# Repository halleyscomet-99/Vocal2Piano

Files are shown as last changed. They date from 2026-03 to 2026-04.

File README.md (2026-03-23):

# Vocal2Piano

An external piano exoskeleton that enables real-time robotic accompaniment by tracking and transcribing vocal performances into physical key strikes.

## System diagram

System diagram

## How it works

1. **Vocal2MIDI_live** listens to a microphone and converts pitch to MIDI in real time. Three modes: single-note melody instrument, singing/voice, or polyphonic chord input.

2. **Vocal2MIDI_file** takes an uploaded audio file, separates vocals from accompaniment if needed (via Demucs), then transcribes to MIDI (via Basic Pitch ONNX).

3. **MIDI2Chords** reads the live melody notes, figures out the key, picks a chord that fits, and sends voicing targets for each board.

4. **MIDI2Piano** takes those chord notes, works out where each board needs to slide to cover them, and sends `MOVE` / `FIRE` commands to the Teensy over USB serial.

5. **Teensy 4.1** moves the two stepper motors and fires the solenoids.

6. **Max/MSP patch** shows the detected notes and key on a visual keyboard in real time, connected to the Vocal2MIDI_live MIDI virtual port.

7. **Web frontend** lets you record live, upload files, see the pipeline status, and play back original vs MIDI side by side.

## Repository structure

```
Vocal2Piano/
├── software/              Python pipeline + React web UI
│   ├── app/               React/Vite frontend
│   ├── engine/            Python scripts
│   │   ├── Vocal2MIDI_live.py
│   │   ├── Vocal2MIDI_file.py
│   │   ├── MIDI2Chords.py
│   │   └── MIDI2Piano.py
│   ├── files/
│   │   ├── input/         uploaded audio (git-ignored)
│   │   └── output/        generated MIDI + stems (git-ignored)
│   └── patch/
│       └── Vocal2MIDI.maxpat    Max/MSP visualization patch
│
├── firmware/              Teensy 4.1 firmware (PlatformIO / C++)
│   ├── platformio.ini
│   └── src/main.cpp
│
└── hardware/
    ├── pcb/               KiCad design files, gerbers, BOM
    └── cad/               Mechanical design, 3D print files
```

## Quick start

### Requirements

- Python 3.11
- Node.js 18+
- PlatformIO CLI

### Python environment

```bash
cd Vocal2Piano
python3.11 -m venv .venv
source .venv/bin/activate

pip install sounddevice aubio librosa scipy python-rtmidi websockets
pip install 'basic-pitch[onnx]' onnxruntime
pip install fastapi uvicorn python-multipart
pip install demucs
pip install pyserial

# optional — better live pitch accuracy
pip install crepe tensorflow
```

### Frontend

```bash
cd software/app
npm install
cp .env.example .env    # set VITE_BACKEND_URL=http://localhost:8000
npm run dev             # opens at http://localhost:3000
```

### Firmware

```bash
cd firmware
pip install platformio
pio run --target upload
pio device monitor --baud 115200
# should print: Voice2Piano Teensy ready
```

### Running the full system

Open four terminals:

```bash
# 1 — file conversion server (File tab in web UI)
source .venv/bin/activate
python software/engine/Vocal2MIDI_file.py --server

# 2 — live pitch detection (match the mode selected in the UI)
python software/engine/Vocal2MIDI_live.py --mode instrument --ws
# or: --mode voice  (singing)
# or: --mode chord  (chords/accompaniment)

# 3 — chord generation
python software/engine/MIDI2Chords.py

# 4 — sends commands to Teensy
python software/engine/MIDI2Piano.py --live
```

Open `http://localhost:3000`.

For Max/MSP: open `software/patch/Vocal2MIDI.maxpat`, set the MIDI input to `Voice2Piano_Layer1`.

## Hardware

Two driver boards (15 solenoids each) slide on independent linear rails driven by NEMA17 steppers via TMC2209 drivers. A Teensy 4.1 controls both boards and both motors over a single USB connection.

### PCB

See [`hardware/pcb/README.md`](hardware/pcb/README.md) for fabrication files, BOM, and assembly instructions.

### CAD / Mechanical

See [`hardware/cad/README.md`](hardware/cad/README.md) for the full mechanical design, system animation, and 3D printable parts with print settings.

## Calibrating rail movement

After flashing the firmware, check that the boards move the right distance:

```bash
# in the Teensy serial monitor:
HOME
MOVE R 12 100
```

Measure the actual travel. It should be 12 × the semitone spacing on your piano (roughly 164mm). If it's off, adjust `STEPS_PER_SEMITONE` in `firmware/src/main.cpp` and reflash.

## Training on real music

MIDI2Chords ships with hand-tuned chord transition weights. To replace them with weights learned from actual MIDI files:

```bash
python software/engine/MIDI2Chords.py --train software/files/input/
# writes learned_transitions.json, loaded automatically next run
```

## Author

Chenwan Halley Zhong — MS Robotics, Northwestern University

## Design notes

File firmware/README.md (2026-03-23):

# Firmware

Teensy 4.1 firmware. Receives serial commands from `MIDI2Piano.py` and controls two solenoid driver boards and two stepper motors.

Built with [PlatformIO](https://platformio.org/).

## Build and flash

```bash
pip install platformio
cd firmware
pio run --target upload
pio device monitor --baud 115200
```

If VS Code shows red squiggles on the includes, run `pio init --ide vscode` once to generate the IntelliSense config. This doesn't affect compilation.

## Pin assignments

| Pin | Signal |
|-----|---|
| 2 | STEP_1 (right stepper) |
| 3 | DIR_1 |
| 4 | STEP_2 (left stepper) |
| 5 | DIR_2 |
| 6 | EN (shared, active LOW) |
| 7 | STOP_1 (right endstop) |
| 8 | STOP_2 (left endstop) |
| 10 | CS (shared 74HC595 latch) |
| 11 | SER_A (right board data) |
| 12 | SER_B (left board data) |
| 13 | SCK (shared clock) |

Both driver boards share SCK and CS. SER_A and SER_B are clocked together on every update so both boards latch simultaneously.

## Serial protocol

115200 baud, ASCII, newline-terminated. Used by `MIDI2Piano.py` — you don't normally need to type these manually.

```
MOVE R <semitone_offset> <rpm>   move right board to offset from home
MOVE L <semitone_offset> <rpm>   move left board
FIRE R <0xMASK> <hold_ms>        fire right solenoids (auto-release after hold_ms)
FIRE L <0xMASK> <hold_ms>        fire left solenoids
RELEASE R / RELEASE L            release immediately
HOME                             home both rails to endstops
STATUS                           reply: STATUS R <pos> L <pos>
```

Solenoid mask is 15-bit: bit 0 = SOL 1, bit 14 = SOL 15. Example: `0x0015` = SOL 1 + SOL 3 + SOL 5.

## Calibrating steps per semitone

`STEPS_PER_SEMITONE` in `src/main.cpp` needs to match your physical setup.

Send `HOME` then `MOVE R 12 100`, and measure how far the board actually moved. It should travel 12 piano semitone spacings (roughly 164mm for a standard piano). Calculate:

```
new value = 1096 × (164 / actual_mm)
```

Update the constant and reflash.

The default of 1096 assumes a NEMA17 with GT2 belt, 20-tooth pulley, 1/16 microstepping. Adjust if your setup differs.

## Dependencies

PlatformIO installs these automatically:

- `waspinator/AccelStepper` — non-blocking stepper control
- `framework-arduinoteensy` — Teensy Arduino core

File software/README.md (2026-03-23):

# Software

Python pipeline and React web UI.

## Structure

```
software/
├── app/                   React/Vite web frontend
│   ├── src/
│   │   ├── components/
│   │   │   ├── FileMode.jsx       file upload UI
│   │   │   ├── LiveMode.jsx       live recording UI
│   │   │   ├── Piano88.jsx        88-key canvas piano (mono + polyphonic)
│   │   │   ├── Waveform.jsx       audio waveform renderer
│   │   │   └── TrackPlayer.jsx    multi-track playback
│   │   ├── hooks/
│   │   │   └── usePitchDetect.js  WebSocket + browser pitch detection
│   │   └── utils/
│   │       └── midiUtils.js       MIDI encoding + Tone.js playback
│   └── .env                       VITE_BACKEND_URL=http://localhost:8000
│
├── engine/
│   ├── Vocal2MIDI_live.py         real-time mic → MIDI
│   ├── Vocal2MIDI_file.py         audio file → MIDI (HTTP server)
│   ├── MIDI2Chords.py             melody → chord notes
│   └── MIDI2Piano.py              chord notes → Teensy serial commands
│
├── files/
│   ├── input/                     uploaded audio (git-ignored)
│   └── output/                    MIDI files + separated stems (git-ignored)
│
└── patch/
    └── Vocal2MIDI.maxpat          Max/MSP visualization patch
```

## Engine scripts

### `Vocal2MIDI_live.py`

Reads from the microphone and outputs MIDI to a virtual port (`Voice2Piano_Layer1`). Also starts a WebSocket server so the web UI can receive the same pitch data.

Three modes:

| Mode | Algorithm | Good for | Latency |
|---|---|---|---|
| `instrument` | CREPE neural net + aubio fallback | piano, guitar | ~100ms |
| `voice` | CREPE + pYIN fallback | singing, humming | ~200ms |
| `chord` | CQT 88-bin peak detection | chords, accompaniment | ~200ms |

```bash
python software/engine/Vocal2MIDI_live.py --mode instrument --ws
python software/engine/Vocal2MIDI_live.py --mode voice --ws
python software/engine/Vocal2MIDI_live.py --mode chord --ws
```

`--ws` opens a WebSocket on `localhost:8765`. The web UI auto-connects and uses the Python pitch results instead of browser autocorrelation. Falls back to browser if the socket isn't available.

Install CREPE for better accuracy (optional):
```bash
pip install crepe tensorflow
```

Detection events are also written to `layer2_queue`, which `MIDI2Chords.py` reads from when running in `--live` mode.

### `Vocal2MIDI_file.py`

Converts uploaded audio files to MIDI. Runs as an HTTP server for the web UI.

```bash
python software/engine/Vocal2MIDI_file.py --server
python software/engine/Vocal2MIDI_file.py song.mp3         # CLI
```

Source type is either auto-detected or user-specified:

| Type | How it's processed |
|---|---|
| `voice` | pYIN extracts the melody line |
| `instrumental` | Basic Pitch ONNX transcribes polyphonically |
| `mixed` | Demucs separates stems, Basic Pitch runs on the accompaniment |

The SSE stream (`POST /convert/stream`) sends pipeline step events as they happen, so the web UI progress bar updates in real time. Stems (vocals + accompaniment) are saved and served via `GET /files/{filename}`.

### `MIDI2Chords.py`

Reads melody notes from `layer2_queue`, works out the current key, picks a chord using a Markov chain, and sends voicing targets to `harmony_queue`.

```bash
python software/engine/MIDI2Chords.py             # test run (C major scale)
python software/engine/MIDI2Chords.py --train software/files/input/
```

The chord transition weights are marked `# [RULE]` (fixed music theory) or `# [TRAIN]` (can be replaced by corpus data). Running `--train` parses MIDI files in the folder and writes `learned_transitions.json`, which is auto-loaded on the next run.

Output events look like:
```python
{
    'right_notes': [60, 64, 67],   # MIDI notes for right board
    'left_notes':  [48],            # MIDI notes for left board
    'chord': 'V',
    'chord_type': 'dom7',
    'key': 'G major',
}
```

### `MIDI2Piano.py`

Reads from `harmony_queue`, figures out where each board needs to slide to cover the target notes, and sends `MOVE` / `FIRE` commands to the Teensy over USB serial.

```bash
python software/engine/MIDI2Piano.py --live         # connect to MIDI2Chords
python software/engine/MIDI2Piano.py                # standalone test (I–IV–V–vi loop)
python software/engine/MIDI2Piano.py --port /dev/tty.usbmodem12345
```

Auto-detects the Teensy by USB vendor ID. Falls back to simulation mode (prints commands to terminal) if no Teensy is connected — useful for testing the chord logic without hardware.

The rail planner tries every position from −12 to +24 semitones for each board and picks the combination that covers the most chord notes, with a small penalty for large movements.

## Frontend

```bash
cd software/app
npm install
npm run dev    # http://localhost:3000
```

**Live tab** — Pick input mode (Instrument / Voice / Chord), record, then compare the original recording against the MIDI output with waveform tracks. The piano lights up keys in real time.

**File tab** — Pick source type (Auto / Voice / Instrumental / Mixed), drop a file. The pipeline progress updates step by step. For mixed files you get four tracks: original, MIDI output, separated vocals, and separated accompaniment.

## Max/MSP patch

Open `software/patch/Vocal2MIDI.maxpat` in Max/MSP. Set the MIDI input to `Voice2Piano_Layer1` (the virtual port opened by `Vocal2MIDI_live.py`). The patch shows a live 88-key keyboard and a rolling note history.

## Dependencies

```bash
pip install sounddevice aubio librosa scipy python-rtmidi websockets
pip install 'basic-pitch[onnx]' onnxruntime
pip install fastapi uvicorn python-multipart
pip install demucs
pip install pyserial
pip install crepe tensorflow      # optional
pip install music21               # optional, for --train
```

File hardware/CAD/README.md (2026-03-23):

# CAD / Mechanical Design

Mechanical design files for the Vocal2Piano system — linear rail assemblies, solenoid mounts, and the piano interface bracket.

## Contents

```
hardware/cad/
├── assembly/              Full system assembly files
│   └── Vocal2Piano_full_assembly.step
├── simulation/            Animation of the full system
│   └── Vocal2Piano_demo.mp4       solenoids firing + rail movement
├── printable/             3D printable parts
│   ├── solenoid_mount_left.stl
│   ├── solenoid_mount_right.stl
│   ├── rail_bracket_piano.stl
│   ├── rail_end_cap.stl
│   └── teensy_enclosure.stl
└── drawings/              2D reference drawings (PDF)
```

## System animation

`simulation/Vocal2Piano_demo.mp4` shows the full system running:
- Both rails sliding to different positions
- Solenoids firing in response to chord events
- The interplay between left and right boards covering different octaves

## 3D printable parts

All parts are designed for FDM printing. No supports needed unless noted.

| File | Material | Infill | Layer height | Notes |
|---|---|---|---|---|
| `solenoid_mount_left.stl` | PETG | 40% | 0.2mm | Print 2× |
| `solenoid_mount_right.stl` | PETG | 40% | 0.2mm | Print 2× |
| `rail_bracket_piano.stl` | PETG | 50% | 0.2mm | Mounts to piano frame |
| `rail_end_cap.stl` | PLA | 20% | 0.2mm | Print 4× (both ends, both rails) |
| `teensy_enclosure.stl` | PLA | 20% | 0.15mm | Optional |

PETG recommended for parts that contact the solenoids — better heat resistance than PLA under sustained operation.

## Assembly notes

The two rail assemblies are independent and identical in construction. Each holds 15 solenoids spaced at piano key intervals, driven by a NEMA17 stepper on a GT2 belt.

The `rail_bracket_piano.stl` bracket clamps to the piano's key bed frame without adhesive or modification to the instrument.

Refer to the full assembly file (`Vocal2Piano_full_assembly.step`) for part placement and hardware dimensions.

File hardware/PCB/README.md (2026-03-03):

# Vocal2Piano PCB Design

This directory contains the hardware design files for the Vocal2Piano controller board. The system is designed to interface a Teensy 4.1 microcontroller with a 30-channel solenoid driver array and dual stepper motor controllers for automated piano performance.

## Overview

The hardware is split into a modular architecture across the schematic sheets:
* **Main Board:** Integrates a Teensy 4.1 breakout for logic control with a **TPS5430** buck converter. It handles 12V-to-5V power regulation and manages signal distribution across the driver arrays, ensuring stable logic power during high-current solenoid switching.
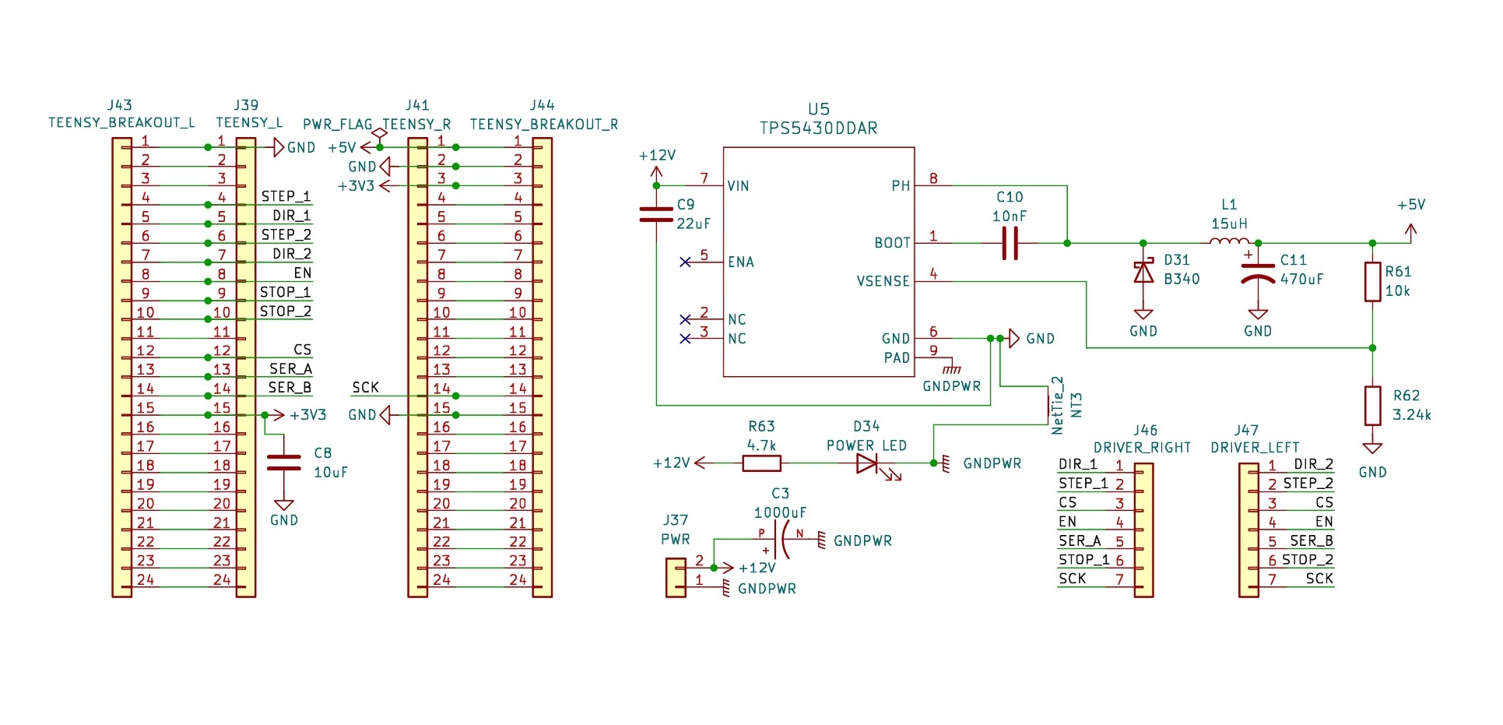
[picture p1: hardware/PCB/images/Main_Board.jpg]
Main_Board

* **Driver Boards (Left/Right):** 30-channel low-side switch array using **IRLZ34N Logic-Level MOSFETs** driven by **SN74HC595** shift registers.
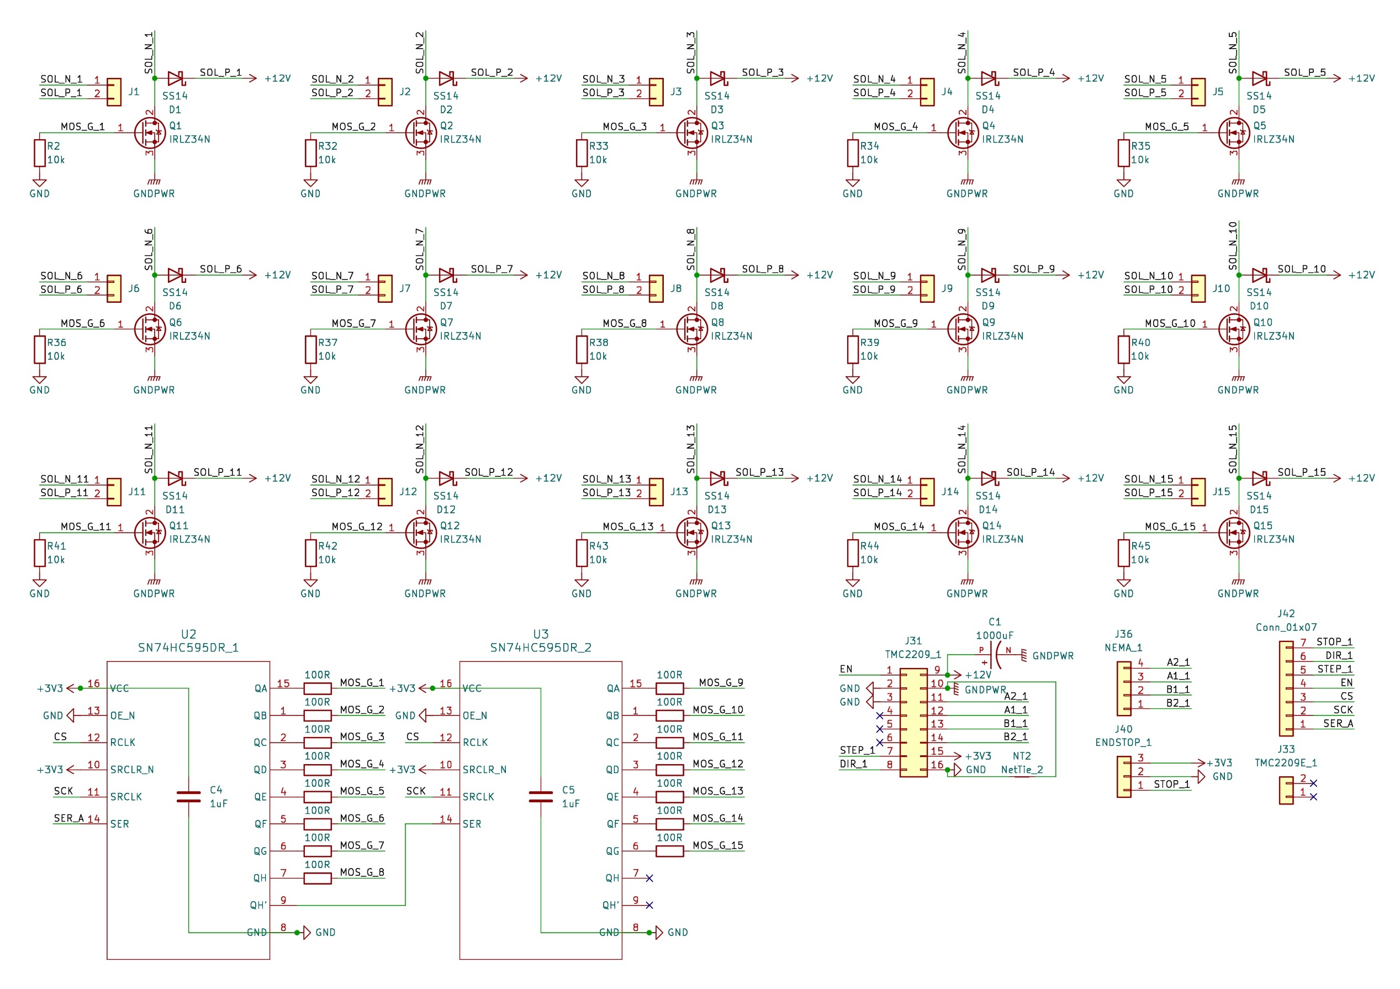
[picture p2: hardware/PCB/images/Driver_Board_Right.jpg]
Driver_Board_Right


## Fabrication Instructions

If you intend to manufacture this board (e.g., via JLCPCB or similar services), follow the steps below using the files provided in the `fabrication/` folder.

### PCB Manufacturing
Use the files located in `fabrication/output/`. 
* **Gerber Files:** All `.gbl`, `.gtl`, `.gbs`, `.gts`, etc., define the copper, mask, and silkscreen layers.
* **Drill Files:** `Vocal2Piano-PTH.drl` (Plated Through Hole) and `Vocal2Piano-NPTH.drl` (Non-Plated Through Hole).
* **Board Specifications:**
    * **Layers:** 2
    * **Copper Weight:** Recommended **2oz** (Essential for 50A power distribution).
    * **Material:** FR-4.

### PCBA (Assembly)
For automated assembly, use the CSV files in the `fabrication/` root:
* **BOM (Bill of Materials):** `BOM.csv`. This includes the LCSC part numbers for the MOSFETs, Shift Registers, and Voltage Regulator.
* **CPL (Component Placement List):** `CPL.csv`. This provides the X/Y coordinates and rotation for SMT components.

## Demonstration

### PCB Layout & 3D Render

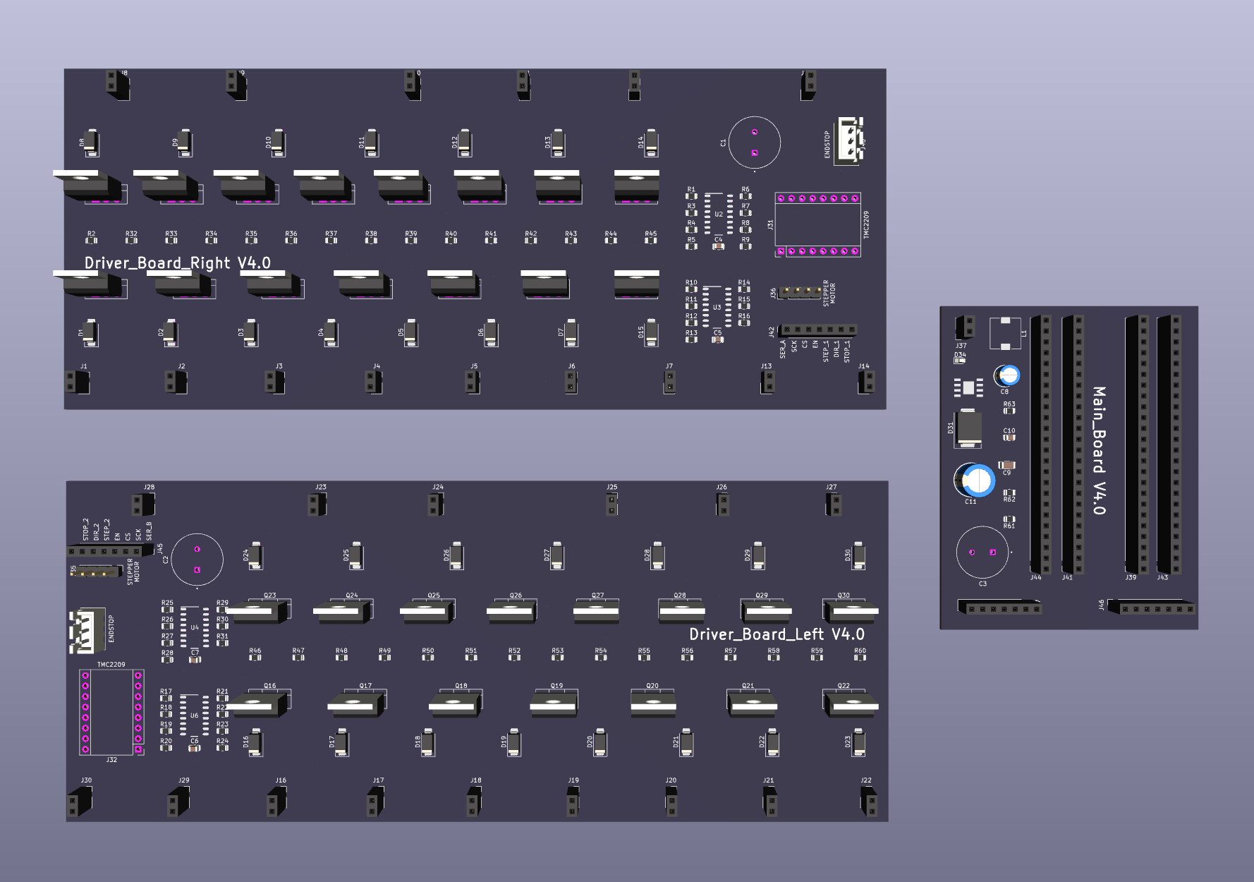
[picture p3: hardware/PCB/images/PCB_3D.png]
PCB_3D


<!-- ### Physical Assembly -->

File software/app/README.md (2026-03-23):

# Voice2Piano — Web Frontend

Real-time and file-based pitch detection to MIDI.
Frontend: React + Vite → Vercel
Backend: FastAPI + Basic Pitch → Render

---

## Quickstart (local)

```bash
# Frontend
npm install
npm run dev
# → http://localhost:3000

# Backend (separate terminal)
cd backend
pip install -r requirements.txt
uvicorn main:app --reload --port 8000
```

Set `VITE_BACKEND_URL=http://localhost:8000` in a `.env` file at the project root.

---

## Deploy Frontend → Vercel

1. Push this repo to GitHub.
2. Go to [vercel.com](https://vercel.com) → New Project → Import repo.
3. Framework Preset: **Vite**
4. Build Command: `npm run build`
5. Output Directory: `dist`
6. Add Environment Variable:
   - Key: `VITE_BACKEND_URL`
   - Value: your Render backend URL (see below)
7. Deploy. Vercel gives you a free permanent URL.

---

## Deploy Backend → Render

1. Go to [render.com](https://render.com) → New Web Service.
2. Connect your GitHub repo.
3. Settings:
   - **Root Directory**: `backend`
   - **Environment**: Python 3
   - **Build Command**: `pip install -r requirements.txt`
   - **Start Command**: `uvicorn main:app --host 0.0.0.0 --port $PORT`
4. Free tier is fine (spins down after inactivity — first request after sleep takes ~30s).
5. Copy the service URL, e.g. `https://voice2piano-api.onrender.com`
6. Paste into Vercel env var `VITE_BACKEND_URL`.

---

## Architecture

```
Browser (Vercel)
  ├── Live Mode
  │   ├── Web Audio API → autocorrelation pitch detection
  │   ├── MIDI note recording (@tonejs/midi)
  │   └── MIDI playback (Tone.js)
  └── File Mode
      ├── Upload audio → POST /convert (Render)
      ├── Backend runs Basic Pitch (Spotify model)
      └── Returns MIDI → playback in browser
```

---

## Tuning

In `src/hooks/usePitchDetect.js`:

| Constant | Effect |
|---|---|
| RMS threshold `0.008` | Lower = more sensitive to quiet input |
| Min freq `21` (MIDI A0) | Change to restrict piano range |

In `Voice2MIDI.py`:

| Constant | Effect |
|---|---|
| `ONSET_THRESHOLD` | Lower = catches faster/softer notes |
| `CONF_MIN` | Lower = more notes, more octave errors |
| `OCTAVE_SHIFT` | Set to 0 if octave correction not needed |

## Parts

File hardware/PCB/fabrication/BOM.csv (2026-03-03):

Designator | Comment | Footprint
L1 | 15uH | L_7.3x7.3_H4.5
J17,J30,J4,J25,J22,J16,J26,J21,J29,J20,J10,J5,J24,J18,J14,J3,J8,J11,J1,J6,J23,J12,J19,J9,J15,J2,J7,J28,J13,J27 | Conn_01x02 | PinSocket_1x02_P2.54mm_Vertical
R19,R14,R23,R21,R25,R9,R26,R11,R4,R28,R31,R7,R24,R5,R17,R6,R29,R1,R8,R3,R12,R22,R20,R27,R18,R13,R15,R10,R16,R30 | 100R | R_0805_2012Metric
C4,C5,C7,C6 | 1uF | C_0805_2012Metric
C1,C3,C2 | 1000uF | CAPPRD500W60D1250H2000
C11 | 470uF | CP_Radial_D8.0mm_P3.50mm
D31 | B340 | D_SMC
D14,D24,D21,D20,D13,D12,D19,D5,D17,D26,D6,D23,D16,D1,D3,D9,D30,D29,D18,D11,D28,D27,D4,D10,D8,D7,D15,D25,D2,D22 | SS14 | D_SMA
J39 | TEENSY_L | PinSocket_1x24_P2.54mm_Vertical
Q13,Q21,Q26,Q18,Q29,Q23,Q19,Q20,Q30,Q17,Q25,Q4,Q22,Q6,Q8,Q9,Q11,Q14,Q5,Q2,Q7,Q1,Q10,Q27,Q12,Q24,Q28,Q16,Q3,Q15 | IRLZ34N | TO-220-3_Vertical
C9 | 22uF | C_1206_3216Metric
R45,R58,R50,R35,R38,R44,R61,R53,R40,R41,R55,R52,R42,R48,R43,R46,R2,R49,R51,R32,R34,R47,R59,R54,R57,R60,R56,R36,R37,R33,R39 | 10k | R_0805_2012Metric
J31 | TMC2209_1 | Pololu_Breakout-16_15.2x20.3mm
J41 | TEENSY_R | PinSocket_1x24_P2.54mm_Vertical
J36 | NEMA_1 | PinHeader_1x04_P2.54mm_Vertical
J44 | TEENSY_BREAKOUT_R | PinSocket_1x24_P2.54mm_Vertical
J42,J45 | Conn_01x07 | PinSocket_1x07_P2.54mm_Vertical
U6 | SN74HC595DR_3 | D0016A_N
U5 | TPS5430DDAR | DDA0008J_NV
J37 | PWR | PinSocket_1x02_P2.54mm_Vertical
R63 | 4.7k | R_0805_2012Metric
U3 | SN74HC595DR_2 | D0016A_N
C8 | 10uF | CP_Radial_D5.0mm_P2.00mm
U2 | SN74HC595DR_1 | D0016A_N
R62 | 3.24k | R_0805_2012Metric
J43 | TEENSY_BREAKOUT_L | PinSocket_1x24_P2.54mm_Vertical
J38 | ENDSTOP_2 | JST_XH_B3B-XH-A_1x03_P2.50mm_Vertical
J46 | DRIVER_RIGHT | PinSocket_1x07_P2.54mm_Vertical
D34 | POWER LED | LED_0603_1608Metric
U4 | SN74HC595DR_4 | D0016A_N
J47 | DRIVER_LEFT | PinSocket_1x07_P2.54mm_Vertical
J40 | ENDSTOP_1 | JST_XH_B3B-XH-A_1x03_P2.50mm_Vertical
C10 | 10nF | C_0805_2012Metric
J35 | NEMA_2 | PinHeader_1x04_P2.54mm_Vertical
J32 | TMC2209_2 | Pololu_Breakout-16_15.2x20.3mm

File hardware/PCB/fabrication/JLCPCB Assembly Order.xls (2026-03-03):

JLCPCB BOM Tool - BOM Matching
BOM name：JLCPCB_BOM_Final-JLCPCB Assembly Order.xlsx |  |  | Download Time：2026-02-27 07:59:04 |  |  |  | * Our matching results are updated in real-time, but stock and prices may change. If it's been over 24 hours, please re-match before placing your order.
PCB Assembled Qty：5 |  |  | Est. Total Price：123.5691
Your BOM |  |  |  |  | Matched Parts |  |  |  |  |  |  | Order Information
Top Designator | Bottom Designator | Comment | Footprint | JLCPCB Part # | Matches | Part # | Manufacturer | Footprint | Description | Category | Warning | JLCPCB Part # | Product link | Lib Type | Qty | Source | Total Price ($)
C1,C3,C2 |  | 1000uF | CAPPRD500W60D1250H2000 |  | Select by System | RVT1000UF10V167RV0083 | KNSCHA | SMD,D8xL10.2mm | -55℃~+105℃ 10.2mm 1000uF 10V 2000hrs@105℃ 230mA@120Hz 8mm ±20% SMD,D8xL10.2mm Aluminum Electrolytic Capacitors - SMD ROHS | Aluminum Electrolytic Capacitors - SMD |  | C5246577 | https://jlcpcb.com/partdetail/KNSCHA-RVT1000UF10V167RV0083/C5246577 | Extended | 16 | 16 JLCPCB | 1.2944
C4,C5,C7,C6 |  | 1uF | C_0805_2012Metric |  | Select by System | CL21B105KBFNNNE | Samsung Electro-Mechanics | 0805 | 1uF 50V X7R ±10% 0805 Multilayer Ceramic Capacitors MLCC - SMD/SMT ROHS | Multilayer Ceramic Capacitors MLCC - SMD/SMT |  | C28323 | https://jlcpcb.com/partdetail/29074-CL21B105KBFNNNE/C28323 | Basic | 30 | 30 JLCPCB | 0.3
C8 |  | 10uF | CP_Radial_D5.0mm_P2.00mm |  | Select by Customer | KS106M050D07RR0VH2FP0 | CX(Dongguan Chengxing Elec) | 插件,D5xL7mm | -40℃~+105℃ 1000hrs@105℃ 10uF 2mm 50V 5mm 7mm ±20% Plugin,D5xL7mm Aluminum Electrolytic Capacitors - Leaded ROHS | Aluminum Electrolytic Capacitors - Leaded |  | C45669 | https://jlcpcb.com/partdetail/46671-KS106M050D07RR0VH2FP0/C45669 | Extended | 10 | 10 JLCPCB | 0.158
C9 |  | 22uF | C_1206_3216Metric |  | Select by System | CL31A226KAHNNNE | Samsung Electro-Mechanics | 1206 | 22uF 25V X5R ±10% 1206 Multilayer Ceramic Capacitors MLCC - SMD/SMT ROHS | Multilayer Ceramic Capacitors MLCC - SMD/SMT |  | C12891 | https://jlcpcb.com/partdetail/13537-CL31A226KAHNNNE/C12891 | Basic | 9 | 9 JLCPCB | 0.4194
C10 |  | 10nF | C_0805_2012Metric |  | Select by System | CL21B103KBANNNC | Samsung Electro-Mechanics | 0805 | 10nF 50V X7R ±10% 0805 Multilayer Ceramic Capacitors MLCC - SMD/SMT ROHS | Multilayer Ceramic Capacitors MLCC - SMD/SMT |  | C1710 | https://jlcpcb.com/partdetail/2062-CL21B103KBANNNC/C1710 | Basic | 20 | 20 JLCPCB | 0.13
C11 |  | 470uF | CP_Radial_D8.0mm_P3.50mm |  | Select by Customer | KM477M035G17RR0VH2FP0 | CX(Dongguan Chengxing Elec) | 插件,D10xL17mm | 10mm 17mm 2000hrs@105℃ 35V 470uF 5mm ±20% Plugin,D10xL17mm Aluminum Electrolytic Capacitors - Leaded ROHS | Aluminum Electrolytic Capacitors - Leaded |  | C2064 | https://jlcpcb.com/partdetail/2416-KM477M035G17RR0VH2FP0/C2064 | Extended | 6 | 6 JLCPCB | 0.5148
D14,D24,D21,D20,D13,D12,D19,D5,D17,D26,D6,D23,D16,D1,D3,D9,D30,D29,D18,D11,D28,D27,D4,D10,D8,D7,D15,D25,D2,D22 |  | SS14 | D_SMA |  | Select by System | SS14 | MDD(Microdiode Semiconductor) | SMA(DO-214AC) | -55℃~+150℃ 1A 25A 300uA@40V 40V 550mV@1A Independent SMA(DO-214AC) Schottky Diodes ROHS | Schottky Diodes |  | C2480 | https://jlcpcb.com/partdetail/MDD_Microdiode_Semiconductor-SS14/C2480 | Basic | 160 | 160 JLCPCB | 2.656
D31 |  | B340 | D_SMC |  | Select by Customer | B340A | MDD(Microdiode Semiconductor) | SMA(DO-214AC) | -50℃~+150℃ 3A 40V 500uA@40V 550mV@3A Independent SMA(DO-214AC) Schottky Diodes ROHS | Schottky Diodes | 1.The comment (B340A) of this part does not match the one (B340) provided in your BOM. Please confirm; | C64982 | https://jlcpcb.com/partdetail/MDD_Microdiode_Semiconductor-B340A/C64982 | Extended | 9 | 9 JLCPCB | 0.3321
D34 |  | POWERLED | LED_0603_1608Metric |  | Select by Customer | KT-0805Y | Hubei KENTO Elec | 0805 | -40℃~+85℃ 1.8V~2.4V 120° 175mcd 40mW 584nm~594nm 596nm Discrete Diode Water Clear Yellow 0805 LED Indication - Discrete ROHS | LED Indication - Discrete | 1.The comment (KT-0805Y) of this part does not match the one (POWERLED) provided in your BOM. Please confirm; | C2296 | https://jlcpcb.com/partdetail/Hubei_KENTOElec-KT0805Y/C2296 | Basic | 20 | 20 JLCPCB | 0.298
J17,J30,J4,J25,J22,J16,J26,J21,J29,J20,J10,J5,J24,J18,J14,J3,J8,J11,J1,J6,J23,J12,J19,J9,J15,J2,J7,J28,J13,J27 |  | Conn_01x02 | PinSocket_1x02_P2.54mm_Vertical |  | Select by Customer | 2.54-1*2P母 | BOOMELE(Boom Precision Elec) | 插件,P=2.54mm | -40℃~+105℃ 1 1x2P 2.54mm 2P 3.3mm 3A Brass Square Hole Through Hole Top Plugin,P=2.54mm Female Headers ROHS | Female Headers |  | C49661 | https://jlcpcb.com/partdetail/50669-2_54_1_2P/C49661 | Extended | 154 | 154 JLCPCB | 6.2216
J38 |  | ENDSTOP_2 | JST_XH_B3B-XH-A_1x03_P2.50mm_Vertical |  | Select by Customer | B3B-XH-A(LF)(SN) | JST | 插件,P=2.5mm | -25℃~+85℃ 1 1x3P 2.5mm 250V 3 3A 3P 5.75mm 7mm 9.9mm Brass K Pin PA66 Through Hole Tin UL94V-0 White XH Plugin,P=2.5mm Wire To Board Connector ROHS | Wire To Board Connector | 1.Multiple lines in the BOM have been matched to the same part. Please check if the matching is correct. ; | C144394 | https://jlcpcb.com/partdetail/JST-B3B_XH_A_LF_SN/C144394 | Extended | 11 | 11 JLCPCB | 0.5544
J40 |  | ENDSTOP_1 | JST_XH_B3B-XH-A_1x03_P2.50mm_Vertical |  | Select by Customer | B3B-XH-A(LF)(SN) | JST | 插件,P=2.5mm | -25℃~+85℃ 1 1x3P 2.5mm 250V 3 3A 3P 5.75mm 7mm 9.9mm Brass K Pin PA66 Through Hole Tin UL94V-0 White XH Plugin,P=2.5mm Wire To Board Connector ROHS | Wire To Board Connector | 1.Multiple lines in the BOM have been matched to the same part. Please check if the matching is correct. ; | C144394 | https://jlcpcb.com/partdetail/JST-B3B_XH_A_LF_SN/C144394 | Extended | 11 | 11 JLCPCB | 0.5544
L1 |  | 15uH | L_7.3x7.3_H4.5 |  | Select by System | YPRH0704-150M | YJYCOIN | SMD,7.3x7.3mm | 1.47A 15uH 81mΩ Magnetic Shielded Inductor ±20% SMD,7.3x7.3mm Power Inductors ROHS | Power Inductors |  | C504017 | https://jlcpcb.com/partdetail/YJYCOIN-YPRH0704150M/C504017 | Extended | 5 | 5 JLCPCB | 1.1755
Q13,Q21,Q26,Q18,Q29,Q23,Q19,Q20,Q30,Q17,Q25,Q4,Q22,Q6,Q8,Q9,Q11,Q14,Q5,Q2,Q7,Q1,Q10,Q27,Q12,Q24,Q28,Q16,Q3,Q15 |  | IRLZ34N | TO-220-3_Vertical |  | Select by Customer | IRLZ34NPBF | Infineon Technologies | TO-220AB | -55℃~+175℃ 1 N-channel 1V 25nC 30A 46mΩ@5V 55V 68W 880pF 94pF TO-220AB MOSFETs ROHS | MOSFETs | 1.The comment (IRLZ34NPBF) of this part does not match the one (IRLZ34N) provided in your BOM. Please confirm; | C513144 | https://jlcpcb.com/partdetail/InfineonTechnologies-IRLZ34NPBF/C513144 | Extended | 150 | 150 JLCPCB | 86.1
R19,R14,R23,R21,R25,R9,R26,R11,R4,R28,R31,R7,R24,R5,R17,R6,R29,R1,R8,R3,R12,R22,R20,R27,R18,R13,R15,R10,R16,R30 |  | 100R | R_0805_2012Metric |  | Select by Customer | 0805W8F1000T5E | UNI-ROYAL(Uniroyal Elec) | 0805 | -55℃~+155℃ 100Ω 125mW 150V Thick Film Resistor ±1% ±100ppm/℃ 0805 Chip Resistor - Surface Mount ROHS | Chip Resistor - Surface Mount | 1.The comment (0805W8F1000T5E) of this part does not match the one (100R) provided in your BOM. Please confirm; | C17408 | https://jlcpcb.com/partdetail/18096-0805W8F1000T5E/C17408 | Basic | 160 | 160 JLCPCB | 0.336
R45,R58,R50,R35,R38,R44,R61,R53,R40,R41,R55,R52,R42,R48,R43,R46,R2,R49,R51,R32,R34,R47,R59,R54,R57,R60,R56,R36,R37,R33,R39 |  | 10k | R_0805_2012Metric |  | Select by Customer | 0805W8F1002T5E | UNI-ROYAL(Uniroyal Elec) | 0805 | -55℃~+155℃ 10kΩ 125mW 150V Thick Film Resistor ±1% ±100ppm/℃ 0805 Chip Resistor - Surface Mount ROHS | Chip Resistor - Surface Mount | 1.The comment (0805W8F1002T5E) of this part does not match the one (10k) provided in your BOM. Please confirm; | C17414 | https://jlcpcb.com/partdetail/18102-0805W8F1002T5E/C17414 | Basic | 165 | 165 JLCPCB | 0.363
R62 |  | 3.24k | R_0805_2012Metric |  | Select by Customer | 0805W8F3241T5E | UNI-ROYAL(Uniroyal Elec) | 0805 | -55℃~+155℃ 125mW 150V 3.24kΩ Thick Film Resistor ±1% ±100ppm/℃ 0805 Chip Resistor - Surface Mount ROHS | Chip Resistor - Surface Mount | 1.The comment (0805W8F3241T5E) of this part does not match the one (3.24k) provided in your BOM. Please confirm; | C17609 | https://jlcpcb.com/partdetail/18297-0805W8F3241T5E/C17609 | Extended | 20 | 20 JLCPCB | 0.048
R63 |  | 4.7k | R_0805_2012Metric |  | Select by Customer | 0805W8F4701T5E | UNI-ROYAL(Uniroyal Elec) | 0805 | -55℃~+155℃ 125mW 150V 4.7kΩ Thick Film Resistor ±1% ±100ppm/℃ 0805 Chip Resistor - Surface Mount ROHS | Chip Resistor - Surface Mount | 1.The comment (0805W8F4701T5E) of this part does not match the one (4.7k) provided in your BOM. Please confirm; | C17673 | https://jlcpcb.com/partdetail/18361-0805W8F4701T5E/C17673 | Basic | 20 | 20 JLCPCB | 0.038
U2 |  | SN74HC595DR_1 | D0016A_N |  | Select by Customer | SN74HC595DR | Texas Instruments | SOIC-16 | -40℃~+85℃ 1 26ns@6V,50pF 29MHz 2V~6V 6mA 74HC 8 Serial-to-Serial or Parallel Tri-State SOIC-16 Shift Registers ROHS | Shift Registers | 1.Multiple lines in the BOM have been matched to the same part. Please check if the matching is correct. ; | C10092 | https://jlcpcb.com/partdetail/TexasInstruments-SN74HC595DR/C10092 | Extended | 20 | 20 JLCPCB | 4.618
U3 |  | SN74HC595DR_2 | D0016A_N |  | Select by Customer | SN74HC595DR | Texas Instruments | SOIC-16 | -40℃~+85℃ 1 26ns@6V,50pF 29MHz 2V~6V 6mA 74HC 8 Serial-to-Serial or Parallel Tri-State SOIC-16 Shift Registers ROHS | Shift Registers | 1.Multiple lines in the BOM have been matched to the same part. Please check if the matching is correct. ; | C10092 | https://jlcpcb.com/partdetail/TexasInstruments-SN74HC595DR/C10092 | Extended | 20 | 20 JLCPCB | 4.618
U4 |  | SN74HC595DR_4 | D0016A_N |  | Select by Customer | SN74HC595DR | Texas Instruments | SOIC-16 | -40℃~+85℃ 1 26ns@6V,50pF 29MHz 2V~6V 6mA 74HC 8 Serial-to-Serial or Parallel Tri-State SOIC-16 Shift Registers ROHS | Shift Registers | 1.Multiple lines in the BOM have been matched to the same part. Please check if the matching is correct. ; | C10092 | https://jlcpcb.com/partdetail/TexasInstruments-SN74HC595DR/C10092 | Extended | 20 | 20 JLCPCB | 4.618
U6 |  | SN74HC595DR_3 | D0016A_N |  | Select by Customer | SN74HC595DR | Texas Instruments | SOIC-16 | -40℃~+85℃ 1 26ns@6V,50pF 29MHz 2V~6V 6mA 74HC 8 Serial-to-Serial or Parallel Tri-State SOIC-16 Shift Registers ROHS | Shift Registers | 1.Multiple lines in the BOM have been matched to the same part. Please check if the matching is correct. ; | C10092 | https://jlcpcb.com/partdetail/TexasInstruments-SN74HC595DR/C10092 | Extended | 20 | 20 JLCPCB | 4.618
U5 |  | TPS5430DDAR | DDA0008J_NV |  | Select by System | TPS5430DDAR | Texas Instruments | SOIC-8-EP | -40℃~+125℃@(TJ) 1 1.221V~32.04V 3A 4.4mA 5.5V~36V 500kHz Adjustable Buck Buck Built-in No SOIC-8-EP DC-DC Converters ROHS | DC-DC Converters |  | C9864 | https://jlcpcb.com/partdetail/TexasInstruments-TPS5430DDAR/C9864 | Basic | 5 | 5 JLCPCB | 3.6035
J31 |  | TMC2209_1 | Pololu_Breakout-16_15.2x20.3mm |  | No matches | No Part Selected
J32 |  | TMC2209_2 | Pololu_Breakout-16_15.2x20.3mm |  | No matches | No Part Selected
J35 |  | NEMA_2 | PinHeader_1x04_P2.54mm_Vertical |  | No matches | No Part Selected
J36 |  | NEMA_1 | PinHeader_1x04_P2.54mm_Vertical |  | No matches | No Part Selected
J37 |  | PWR | PinSocket_1x02_P2.54mm_Vertical |  | No matches | No Part Selected
J39 |  | TEENSY_L | PinSocket_1x24_P2.54mm_Vertical |  | No matches | No Part Selected
J41 |  | TEENSY_R | PinSocket_1x24_P2.54mm_Vertical |  | No matches | No Part Selected
J42,J45 |  | Conn_01x07 | PinSocket_1x07_P2.54mm_Vertical |  | No matches | No Part Selected
J43 |  | TEENSY_BREAKOUT_L | PinSocket_1x24_P2.54mm_Vertical |  | No matches | No Part Selected
J44 |  | TEENSY_BREAKOUT_R | PinSocket_1x24_P2.54mm_Vertical |  | No matches | No Part Selected
J46 |  | DRIVER_RIGHT | PinSocket_1x07_P2.54mm_Vertical |  | No matches | No Part Selected
J47 |  | DRIVER_LEFT | PinSocket_1x07_P2.54mm_Vertical |  | No matches | No Part Selected

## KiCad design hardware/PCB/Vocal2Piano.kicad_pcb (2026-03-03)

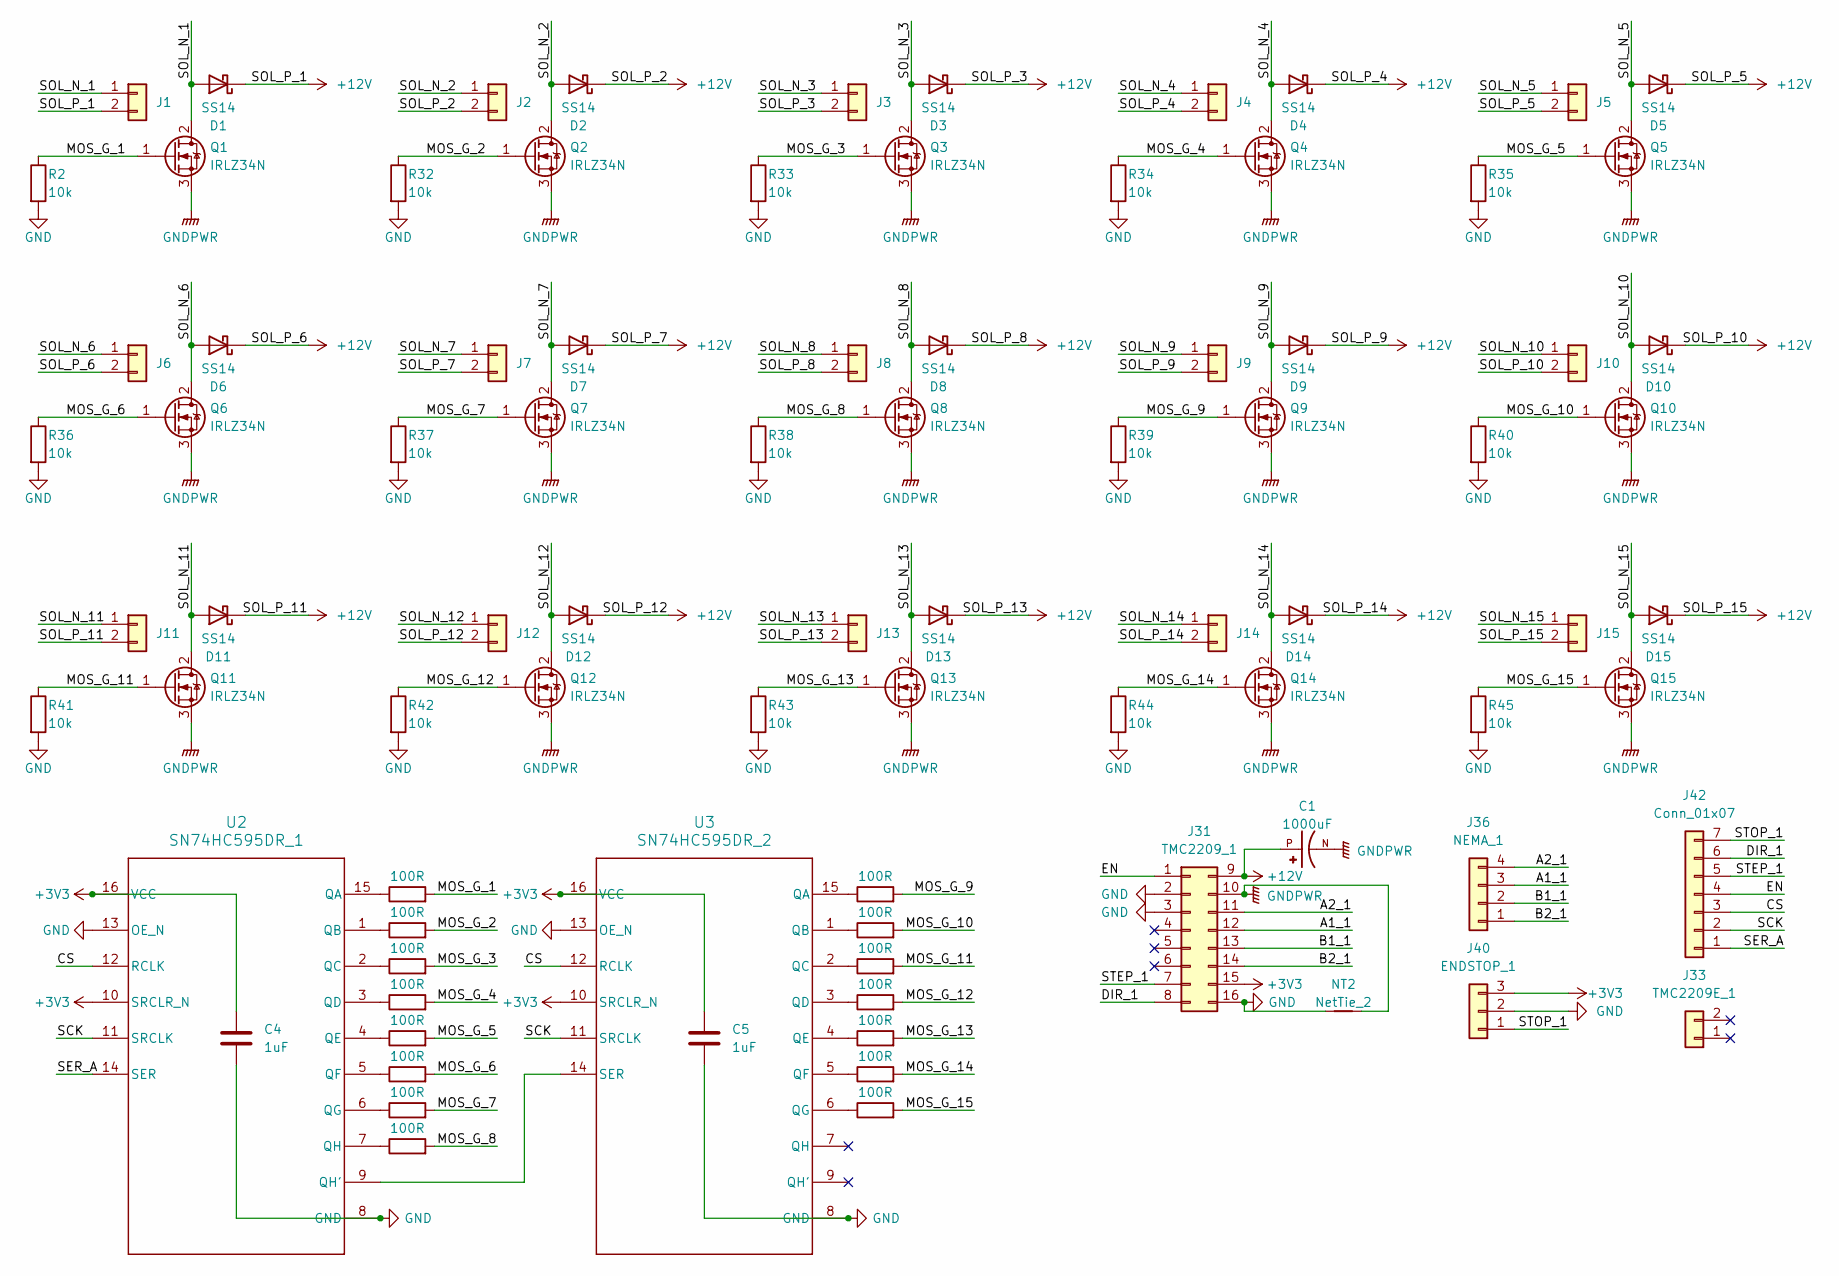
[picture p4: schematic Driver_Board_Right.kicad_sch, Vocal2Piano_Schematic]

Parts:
C1: 1000uF; CAPPRD500W60D1250H2000; PARTREV 20-DEC-19
C4, C5: 1uF; C_0805_2012Metric
D1, D2, D3, D4, D5, D6, D7, D8, D9, D10, D11, D12, D13, D14, D15: SS14; D_SMA
J1, J2, J3, J4, J5, J6, J7, J8, J9, J10, J11, J12, J13, J14, J15: Conn_01x02; PinSocket_1x02_P2.54mm_Vertical
J31: TMC2209_1; Pololu_Breakout-16_15.2x20.3mm
J33: TMC2209E_1; PinSocket_1x02_P2.54mm_Vertical
J36: NEMA_1; PinHeader_1x04_P2.54mm_Vertical
J40: ENDSTOP_1; JST_XH_B3B-XH-A_1x03_P2.50mm_Vertical
J42: Conn_01x07; PinSocket_1x07_P2.54mm_Vertical
NT2: NetTie_2; NetTie-2_SMD_Pad0.5mm
Q1, Q2, Q3, Q4, Q5, Q6, Q7, Q8, Q9, Q10, Q11, Q12, Q13, Q14, Q15: IRLZ34N; TO-220-3_Vertical
R1, R3, R4, R5, R6, R7, R8, R9, R10, R11, R12, R13, R14, R15, R16: 100R; R_0805_2012Metric
R2, R32, R33, R34, R35, R36, R37, R38, R39, R40, R41, R42, R43, R44, R45: 10k; R_0805_2012Metric
U2: SN74HC595DR_1; D0016A_N
U3: SN74HC595DR_2; D0016A_N

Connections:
+3V3: C4.1, C5.1, J31.15 (VDD), J40.3, U2.10 (SRCLR_N), U2.16 (VCC), U3.10 (SRCLR_N), U3.16 (VCC); also elsewhere on the board
+12V: C1.P, D1.1 (K), D2.1 (K), D3.1 (K), D4.1 (K), D5.1 (K), D6.1 (K), D7.1 (K), D8.1 (K), D9.1 (K), D10.1 (K), D11.1 (K), D12.1 (K), D13.1 (K), D14.1 (K), D15.1 (K), J1.2, J2.2, J3.2, J4.2, J5.2, J6.2, J7.2, J8.2, J9.2, J10.2, J11.2, J12.2, J13.2, J14.2, J15.2, J31.9 (VM); also elsewhere on the board
/Driver_Board_Right/A1_1: J31.12 (A1), J36.3
/Driver_Board_Right/A2_1: J31.11 (A2), J36.4
/Driver_Board_Right/B1_1: J31.13 (B1), J36.2
/Driver_Board_Right/B2_1: J31.14 (B2), J36.1
/Driver_Board_Right/CS: J42.3, U2.12 (RCLK), U3.12 (RCLK)
/Driver_Board_Right/DIR_1: J31.8 (DIR), J42.6
/Driver_Board_Right/EN: J31.1 (EN), J42.4
/Driver_Board_Right/MOS_G_1: Q1.1 (G), R1.2, R2.1
/Driver_Board_Right/MOS_G_2: Q2.1 (G), R3.2, R32.1
/Driver_Board_Right/MOS_G_3: Q3.1 (G), R4.2, R33.1
/Driver_Board_Right/MOS_G_4: Q4.1 (G), R5.2, R34.1
/Driver_Board_Right/MOS_G_5: Q5.1 (G), R6.2, R35.1
/Driver_Board_Right/MOS_G_6: Q6.1 (G), R7.2, R36.1
/Driver_Board_Right/MOS_G_7: Q7.1 (G), R8.2, R37.1
/Driver_Board_Right/MOS_G_8: Q8.1 (G), R9.2, R38.1
/Driver_Board_Right/MOS_G_9: Q9.1 (G), R10.2, R39.1
/Driver_Board_Right/MOS_G_10: Q10.1 (G), R11.2, R40.1
/Driver_Board_Right/MOS_G_11: Q11.1 (G), R12.2, R41.1
/Driver_Board_Right/MOS_G_12: Q12.1 (G), R13.2, R42.1
/Driver_Board_Right/MOS_G_13: Q13.1 (G), R14.2, R43.1
/Driver_Board_Right/MOS_G_14: Q14.1 (G), R15.2, R44.1
/Driver_Board_Right/MOS_G_15: Q15.1 (G), R16.2, R45.1
/Driver_Board_Right/SCK: J42.2, U2.11 (SRCLK), U3.11 (SRCLK)
/Driver_Board_Right/SER_A: J42.1, U2.14 (SER)
/Driver_Board_Right/SOL_N_1: D1.2 (A), J1.1, Q1.2 (D)
/Driver_Board_Right/SOL_N_2: D2.2 (A), J2.1, Q2.2 (D)
/Driver_Board_Right/SOL_N_3: D3.2 (A), J3.1, Q3.2 (D)
/Driver_Board_Right/SOL_N_4: D4.2 (A), J4.1, Q4.2 (D)
/Driver_Board_Right/SOL_N_5: D5.2 (A), J5.1, Q5.2 (D)
/Driver_Board_Right/SOL_N_6: D6.2 (A), J6.1, Q6.2 (D)
/Driver_Board_Right/SOL_N_7: D7.2 (A), J7.1, Q7.2 (D)
/Driver_Board_Right/SOL_N_8: D8.2 (A), J8.1, Q8.2 (D)
/Driver_Board_Right/SOL_N_9: D9.2 (A), J9.1, Q9.2 (D)
/Driver_Board_Right/SOL_N_10: D10.2 (A), J10.1, Q10.2 (D)
/Driver_Board_Right/SOL_N_11: D11.2 (A), J11.1, Q11.2 (D)
/Driver_Board_Right/SOL_N_12: D12.2 (A), J12.1, Q12.2 (D)
/Driver_Board_Right/SOL_N_13: D13.2 (A), J13.1, Q13.2 (D)
/Driver_Board_Right/SOL_N_14: D14.2 (A), J14.1, Q14.2 (D)
/Driver_Board_Right/SOL_N_15: D15.2 (A), J15.1, Q15.2 (D)
/Driver_Board_Right/STEP_1: J31.7 (STEP), J42.5
/Driver_Board_Right/STOP_1: J40.1, J42.7
GND: C4.2, C5.2, J31.2 (MS1), J31.3 (MS2), J31.16 (GND), J40.2, NT2.1, R2.2, R32.2, R33.2, R34.2, R35.2, R36.2, R37.2, R38.2, R39.2, R40.2, R41.2, R42.2, R43.2, R44.2, R45.2, U2.8 (GND), U2.13 (OE_N), U3.8 (GND), U3.13 (OE_N); also elsewhere on the board
GNDPWR: C1.N, J31.10 (GND), NT2.2, Q1.3 (S), Q2.3 (S), Q3.3 (S), Q4.3 (S), Q5.3 (S), Q6.3 (S), Q7.3 (S), Q8.3 (S), Q9.3 (S), Q10.3 (S), Q11.3 (S), Q12.3 (S), Q13.3 (S), Q14.3 (S), Q15.3 (S); also elsewhere on the board
unnamed: R1.1, U2.15 (QA)
unnamed: R3.1, U2.1 (QB)
unnamed: R4.1, U2.2 (QC)
unnamed: R5.1, U2.3 (QD)
unnamed: R6.1, U2.4 (QE)
unnamed: R7.1, U2.5 (QF)
unnamed: R8.1, U2.6 (QG)
unnamed: U2.9 (QH'), U3.14 (SER)
unnamed: R9.1, U2.7 (QH)
unnamed: R10.1, U3.15 (QA)
unnamed: R11.1, U3.1 (QB)
unnamed: R12.1, U3.2 (QC)
unnamed: R13.1, U3.3 (QD)
unnamed: R14.1, U3.4 (QE)
unnamed: R15.1, U3.5 (QF)
unnamed: R16.1, U3.6 (QG)

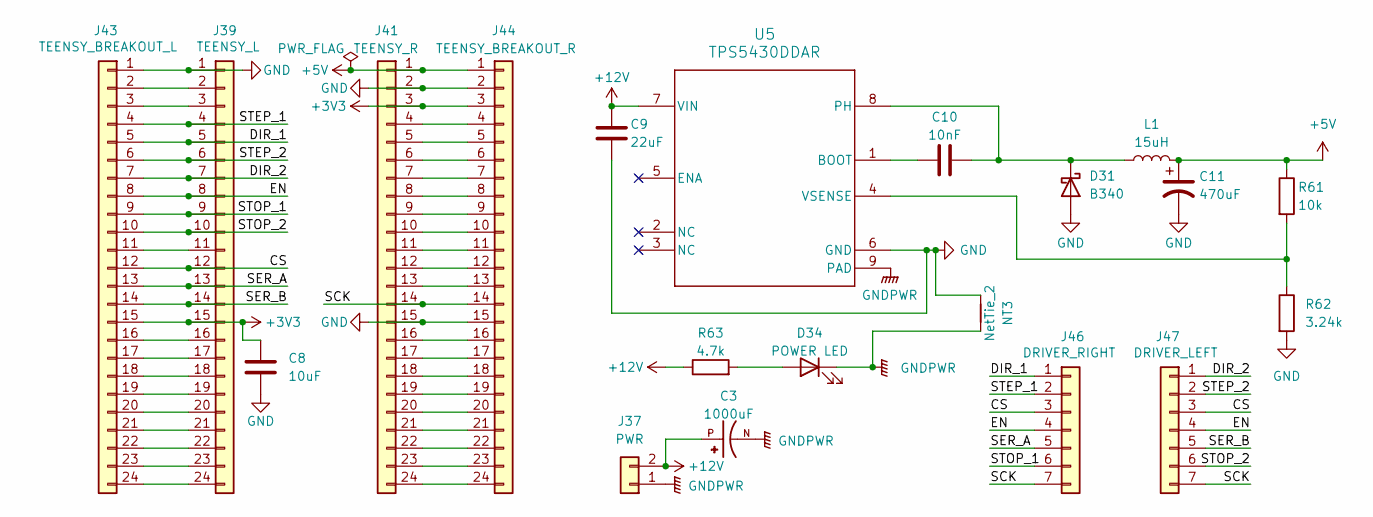
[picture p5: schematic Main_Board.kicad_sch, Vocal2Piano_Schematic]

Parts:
C3: 1000uF; CAPPRD500W60D1250H2000; PARTREV 20-DEC-19
C8: 10uF; CP_Radial_D5.0mm_P2.00mm
C9: 22uF; C_1206_3216Metric
C10: 10nF; C_0805_2012Metric
C11: 470uF; CP_Radial_D8.0mm_P3.50mm
D31: B340; D_SMC
D34: POWER LED; LED_0603_1608Metric
J37: PWR; PinSocket_1x02_P2.54mm_Vertical
J39: TEENSY_L; PinSocket_1x24_P2.54mm_Vertical
J41: TEENSY_R; PinSocket_1x24_P2.54mm_Vertical
J43: TEENSY_BREAKOUT_L; PinSocket_1x24_P2.54mm_Vertical
J44: TEENSY_BREAKOUT_R; PinSocket_1x24_P2.54mm_Vertical
J46: DRIVER_RIGHT; PinSocket_1x07_P2.54mm_Vertical
J47: DRIVER_LEFT; PinSocket_1x07_P2.54mm_Vertical
L1: 15uH; L_7.3x7.3_H4.5
NT3: NetTie_2; NetTie-2_SMD_Pad0.5mm
R61: 10k; R_0805_2012Metric
R62: 3.24k; R_0805_2012Metric
R63: 4.7k; R_0805_2012Metric
U5: TPS5430DDAR; DDA0008J_NV

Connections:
+3V3: C8.1, J39.15, J41.3, J43.15, J44.3; also elsewhere on the board
+5V: C11.1, J41.1, J44.1, L1.2, R61.1
+12V: C3.P, C9.1, J37.2, R63.1, U5.7 (VIN); also elsewhere on the board
/Main_Board/CS: J39.12, J43.12, J46.3, J47.3
/Main_Board/DIR_1: J39.5, J43.5, J46.1
/Main_Board/DIR_2: J39.7, J43.7, J47.1
/Main_Board/EN: J39.8, J43.8, J46.4, J47.4
/Main_Board/SCK: J41.14, J44.14, J46.7, J47.7
/Main_Board/SER_A: J39.13, J43.13, J46.5
/Main_Board/SER_B: J39.14, J43.14, J47.5
/Main_Board/STEP_1: J39.4, J43.4, J46.2
/Main_Board/STEP_2: J39.6, J43.6, J47.2
/Main_Board/STOP_1: J39.9, J43.9, J46.6
/Main_Board/STOP_2: J39.10, J43.10, J47.6
GND: C8.2, C9.2, C11.2, D31.2 (A), J39.1, J41.2, J41.15, J43.1, J44.2, J44.15, NT3.1, R62.2, U5.6 (GND); also elsewhere on the board
GNDPWR: C3.N, D34.1 (K), J37.1, NT3.2, U5.9 (PAD); also elsewhere on the board
unnamed: C10.2, D31.1 (K), L1.1, U5.8 (PH)
unnamed: D34.2 (A), R63.2
unnamed: J39.2, J43.2
unnamed: J39.3, J43.3
unnamed: J39.11, J43.11
unnamed: J39.16, J43.16
unnamed: J39.17, J43.17
unnamed: J39.18, J43.18
unnamed: J39.19, J43.19
unnamed: J39.20, J43.20
unnamed: J39.21, J43.21
unnamed: J39.22, J43.22
unnamed: J39.23, J43.23
unnamed: J39.24, J43.24
unnamed: J41.4, J44.4
unnamed: J41.5, J44.5
unnamed: J41.6, J44.6
unnamed: J41.7, J44.7
unnamed: J41.8, J44.8
unnamed: J41.9, J44.9
unnamed: J41.10, J44.10
unnamed: J41.11, J44.11
unnamed: J41.12, J44.12
unnamed: J41.13, J44.13
unnamed: J41.16, J44.16
unnamed: J41.17, J44.17
unnamed: J41.18, J44.18
unnamed: J41.19, J44.19
unnamed: J41.20, J44.20
unnamed: J41.21, J44.21
unnamed: J41.22, J44.22
unnamed: J41.23, J44.23
unnamed: J41.24, J44.24
unnamed: C10.1, U5.1 (BOOT)
unnamed: R61.2, R62.1, U5.4 (VSENSE)

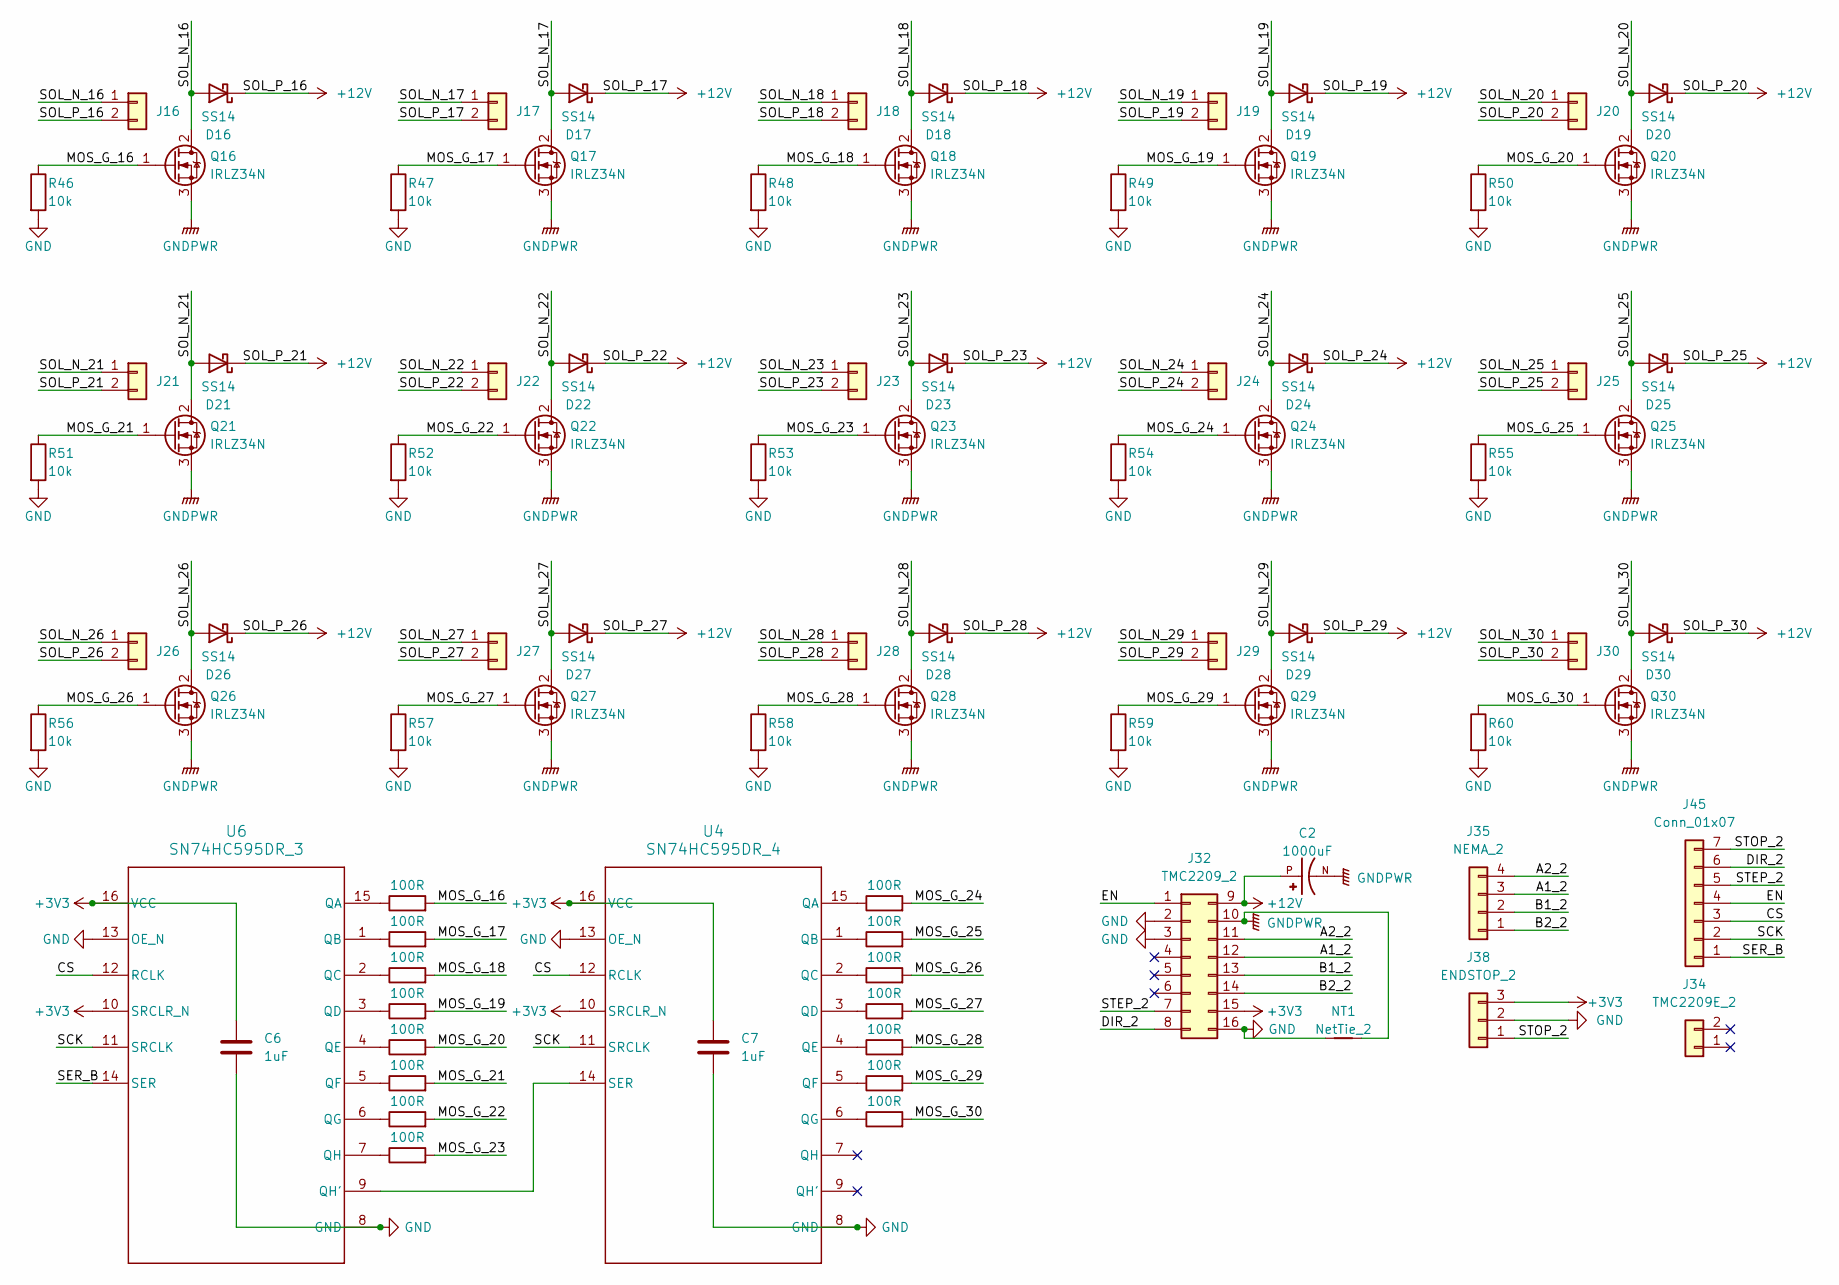
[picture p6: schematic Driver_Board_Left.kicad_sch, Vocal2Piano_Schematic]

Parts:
C2: 1000uF; CAPPRD500W60D1250H2000; PARTREV 20-DEC-19
C6, C7: 1uF; C_0805_2012Metric
D16, D17, D18, D19, D20, D21, D22, D23, D24, D25, D26, D27, D28, D29, D30: SS14; D_SMA
J16, J17, J18, J19, J20, J21, J22, J23, J24, J25, J26, J27, J28, J29, J30: Conn_01x02; PinSocket_1x02_P2.54mm_Vertical
J32: TMC2209_2; Pololu_Breakout-16_15.2x20.3mm
J34: TMC2209E_2; PinSocket_1x02_P2.54mm_Vertical
J35: NEMA_2; PinHeader_1x04_P2.54mm_Vertical
J38: ENDSTOP_2; JST_XH_B3B-XH-A_1x03_P2.50mm_Vertical
J45: Conn_01x07; PinSocket_1x07_P2.54mm_Vertical
NT1: NetTie_2; NetTie-2_SMD_Pad0.5mm
Q16, Q17, Q18, Q19, Q20, Q21, Q22, Q23, Q24, Q25, Q26, Q27, Q28, Q29, Q30: IRLZ34N; TO-220-3_Vertical
R17, R18, R19, R20, R21, R22, R23, R24, R25, R26, R27, R28, R29, R30, R31: 100R; R_0805_2012Metric
R46, R47, R48, R49, R50, R51, R52, R53, R54, R55, R56, R57, R58, R59, R60: 10k; R_0805_2012Metric
U4: SN74HC595DR_4; D0016A_N
U6: SN74HC595DR_3; D0016A_N

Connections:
+3V3: C6.1, C7.1, J32.15 (VDD), J38.3, U4.10 (SRCLR_N), U4.16 (VCC), U6.10 (SRCLR_N), U6.16 (VCC); also elsewhere on the board
+12V: C2.P, D16.1 (K), D17.1 (K), D18.1 (K), D19.1 (K), D20.1 (K), D21.1 (K), D22.1 (K), D23.1 (K), D24.1 (K), D25.1 (K), D26.1 (K), D27.1 (K), D28.1 (K), D29.1 (K), D30.1 (K), J16.2, J17.2, J18.2, J19.2, J20.2, J21.2, J22.2, J23.2, J24.2, J25.2, J26.2, J27.2, J28.2, J29.2, J30.2, J32.9 (VM); also elsewhere on the board
/Driver_Board_Left/A1_2: J32.12 (A1), J35.3
/Driver_Board_Left/A2_2: J32.11 (A2), J35.4
/Driver_Board_Left/B1_2: J32.13 (B1), J35.2
/Driver_Board_Left/B2_2: J32.14 (B2), J35.1
/Driver_Board_Left/CS: J45.3, U4.12 (RCLK), U6.12 (RCLK)
/Driver_Board_Left/DIR_2: J32.8 (DIR), J45.6
/Driver_Board_Left/EN: J32.1 (EN), J45.4
/Driver_Board_Left/MOS_G_16: Q16.1 (G), R17.2, R46.1
/Driver_Board_Left/MOS_G_17: Q17.1 (G), R18.2, R47.1
/Driver_Board_Left/MOS_G_18: Q18.1 (G), R19.2, R48.1
/Driver_Board_Left/MOS_G_19: Q19.1 (G), R20.2, R49.1
/Driver_Board_Left/MOS_G_20: Q20.1 (G), R21.2, R50.1
/Driver_Board_Left/MOS_G_21: Q21.1 (G), R22.2, R51.1
/Driver_Board_Left/MOS_G_22: Q22.1 (G), R23.2, R52.1
/Driver_Board_Left/MOS_G_23: Q23.1 (G), R24.2, R53.1
/Driver_Board_Left/MOS_G_24: Q24.1 (G), R25.2, R54.1
/Driver_Board_Left/MOS_G_25: Q25.1 (G), R26.2, R55.1
/Driver_Board_Left/MOS_G_26: Q26.1 (G), R27.2, R56.1
/Driver_Board_Left/MOS_G_27: Q27.1 (G), R28.2, R57.1
/Driver_Board_Left/MOS_G_28: Q28.1 (G), R29.2, R58.1
/Driver_Board_Left/MOS_G_29: Q29.1 (G), R30.2, R59.1
/Driver_Board_Left/MOS_G_30: Q30.1 (G), R31.2, R60.1
/Driver_Board_Left/SCK: J45.2, U4.11 (SRCLK), U6.11 (SRCLK)
/Driver_Board_Left/SER_B: J45.1, U6.14 (SER)
/Driver_Board_Left/SOL_N_16: D16.2 (A), J16.1, Q16.2 (D)
/Driver_Board_Left/SOL_N_17: D17.2 (A), J17.1, Q17.2 (D)
/Driver_Board_Left/SOL_N_18: D18.2 (A), J18.1, Q18.2 (D)
/Driver_Board_Left/SOL_N_19: D19.2 (A), J19.1, Q19.2 (D)
/Driver_Board_Left/SOL_N_20: D20.2 (A), J20.1, Q20.2 (D)
/Driver_Board_Left/SOL_N_21: D21.2 (A), J21.1, Q21.2 (D)
/Driver_Board_Left/SOL_N_22: D22.2 (A), J22.1, Q22.2 (D)
/Driver_Board_Left/SOL_N_23: D23.2 (A), J23.1, Q23.2 (D)
/Driver_Board_Left/SOL_N_24: D24.2 (A), J24.1, Q24.2 (D)
/Driver_Board_Left/SOL_N_25: D25.2 (A), J25.1, Q25.2 (D)
/Driver_Board_Left/SOL_N_26: D26.2 (A), J26.1, Q26.2 (D)
/Driver_Board_Left/SOL_N_27: D27.2 (A), J27.1, Q27.2 (D)
/Driver_Board_Left/SOL_N_28: D28.2 (A), J28.1, Q28.2 (D)
/Driver_Board_Left/SOL_N_29: D29.2 (A), J29.1, Q29.2 (D)
/Driver_Board_Left/SOL_N_30: D30.2 (A), J30.1, Q30.2 (D)
/Driver_Board_Left/STEP_2: J32.7 (STEP), J45.5
/Driver_Board_Left/STOP_2: J38.1, J45.7
GND: C6.2, C7.2, J32.2 (MS1), J32.3 (MS2), J32.16 (GND), J38.2, NT1.1, R46.2, R47.2, R48.2, R49.2, R50.2, R51.2, R52.2, R53.2, R54.2, R55.2, R56.2, R57.2, R58.2, R59.2, R60.2, U4.8 (GND), U4.13 (OE_N), U6.8 (GND), U6.13 (OE_N); also elsewhere on the board
GNDPWR: C2.N, J32.10 (GND), NT1.2, Q16.3 (S), Q17.3 (S), Q18.3 (S), Q19.3 (S), Q20.3 (S), Q21.3 (S), Q22.3 (S), Q23.3 (S), Q24.3 (S), Q25.3 (S), Q26.3 (S), Q27.3 (S), Q28.3 (S), Q29.3 (S), Q30.3 (S); also elsewhere on the board
unnamed: R25.1, U4.15 (QA)
unnamed: R26.1, U4.1 (QB)
unnamed: R27.1, U4.2 (QC)
unnamed: R28.1, U4.3 (QD)
unnamed: R29.1, U4.4 (QE)
unnamed: R30.1, U4.5 (QF)
unnamed: R31.1, U4.6 (QG)
unnamed: U4.14 (SER), U6.9 (QH')
unnamed: R17.1, U6.15 (QA)
unnamed: R18.1, U6.1 (QB)
unnamed: R19.1, U6.2 (QC)
unnamed: R20.1, U6.3 (QD)
unnamed: R21.1, U6.4 (QE)
unnamed: R22.1, U6.5 (QF)
unnamed: R23.1, U6.6 (QG)
unnamed: R24.1, U6.7 (QH)

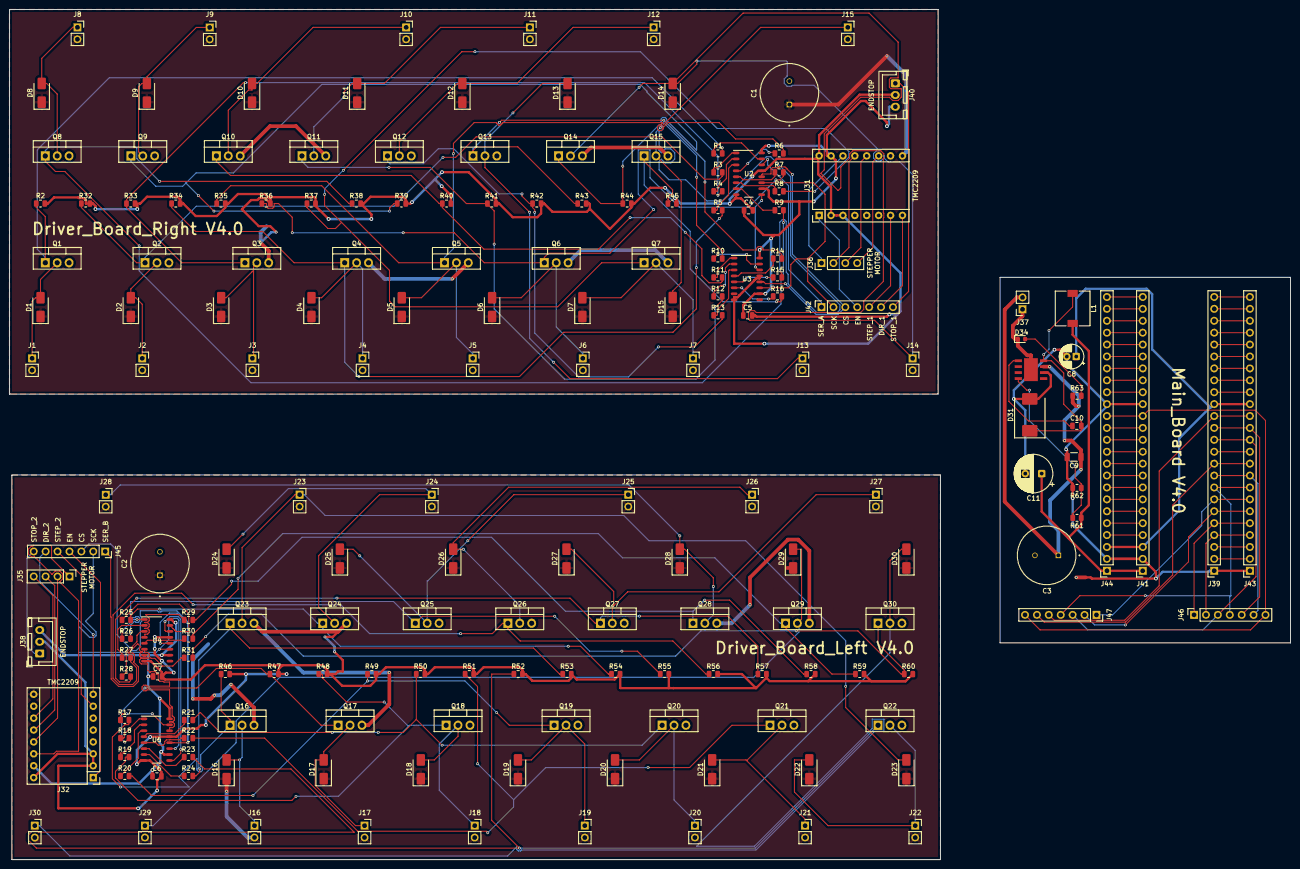
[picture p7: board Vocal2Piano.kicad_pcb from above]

Board: 2 copper layers, 273.3 x 181.4 mm, 190 parts (0 on the bottom side), 165 nets.

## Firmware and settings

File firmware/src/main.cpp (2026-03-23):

/*
 * Voice2Piano -- Teensy 4.1 Firmware
 * ====================================
 * Controls two solenoid driver boards (74HC595 shift registers)
 * and two stepper motors (TMC2209) on linear rails.
 *
 * PIN ASSIGNMENTS
 * ---------------
 *  Pin 2   STEP_1     Right stepper pulse
 *  Pin 3   DIR_1      Right stepper direction
 *  Pin 4   STEP_2     Left stepper pulse
 *  Pin 5   DIR_2      Left stepper direction
 *  Pin 6   EN         Shared stepper enable (active LOW)
 *  Pin 7   STOP_1     Right endstop (INPUT_PULLUP, LOW = triggered)
 *  Pin 8   STOP_2     Left endstop
 *  Pin 10  CS         Shared 74HC595 latch (rising edge latches both boards)
 *  Pin 11  SER_A      Right board shift register data
 *  Pin 12  SER_B      Left board shift register data
 *  Pin 13  SCK        Shared shift register clock
 *
 * SHIFT REGISTER TOPOLOGY
 * ------------------------
 * Right board: two 74HC595 daisy-chained (SOL_1-15), driven by SER_A.
 * Left board:  two 74HC595 daisy-chained (SOL_16-30), driven by SER_B.
 * SCK and CS are shared. Both boards are clocked simultaneously on
 * every update -- CS rising edge latches both at the same time.
 * This means updateBoards() always writes both masks together.
 *
 * COMMAND PROTOCOL  (USB Serial, 115200 baud, newline terminated)
 * ---------------------------------------------------------------
 *  MOVE R <offset> <rpm>    Move right board to semitone offset from home
 *  MOVE L <offset> <rpm>    Move left board
 *  FIRE R <0xMASK> <ms>     Fire right solenoids, auto-release after ms
 *  FIRE L <0xMASK> <ms>     Fire left solenoids
 *  RELEASE R                Release right solenoids immediately
 *  RELEASE L                Release left solenoids immediately
 *  HOME                     Home both rails (move to endstop, zero position)
 *  STATUS                   Reply: STATUS R <pos> L <pos>
 *
 * SOLENOID MASK FORMAT
 * --------------------
 *  15-bit integer, bit 0 = SOL_1 (first solenoid), bit 14 = SOL_15.
 *  Example: 0x0015 = binary 000000000010101 = SOL_1 + SOL_3 + SOL_5
 *
 * STEPS_PER_SEMITONE CALIBRATION
 * --------------------------------
 *  Measure: command MOVE R 12, measure actual rail travel in mm.
 *  Expected: 12 * (piano semitone spacing) mm.
 *  Piano semitone spacing ≈ 13.7 mm (white key width 23.5mm * 7/12).
 *  With NEMA17 + GT2 belt + 20-tooth pulley + 1/16 microstepping:
 *    mm per step = (20 teeth * 2mm pitch) / (200 steps * 16 ustep) = 0.0125mm
 *    steps per semitone = 13.7 / 0.0125 ≈ 1096
 *  Adjust STEPS_PER_SEMITONE until MOVE R 12 travels exactly 12 semitones.
 */

#include <Arduino.h>
#include <AccelStepper.h>

// ============================================================
// PIN DEFINITIONS
// ============================================================

constexpr uint8_t PIN_STEP_R = 2;
constexpr uint8_t PIN_DIR_R  = 3;
constexpr uint8_t PIN_STEP_L = 4;
constexpr uint8_t PIN_DIR_L  = 5;
constexpr uint8_t PIN_EN     = 6;   // active LOW
constexpr uint8_t PIN_STOP_R = 7;   // INPUT_PULLUP, LOW = triggered
constexpr uint8_t PIN_STOP_L = 8;
constexpr uint8_t PIN_CS     = 10;  // 74HC595 latch (shared)
constexpr uint8_t PIN_SER_A  = 11;  // right board data
constexpr uint8_t PIN_SER_B  = 12;  // left board data
constexpr uint8_t PIN_SCK    = 13;  // clock (shared)


// ============================================================
// STEPPER CONFIGURATION
// ============================================================

// Adjust this value to match your hardware (see calibration note above)
constexpr int STEPS_PER_SEMITONE = 1096;

constexpr float MAX_SPEED  = 20000.0f;  // steps/sec
constexpr float ACCEL      = 8000.0f;   // steps/sec^2
constexpr float HOME_SPEED = 3000.0f;   // slower during homing


// ============================================================
// SOLENOID CONFIGURATION
// ============================================================

constexpr int DEFAULT_HOLD_MS = 80;     // auto-release time


// ============================================================
// STATE
// ============================================================

AccelStepper stepperR(AccelStepper::DRIVER, PIN_STEP_R, PIN_DIR_R);
AccelStepper stepperL(AccelStepper::DRIVER, PIN_STEP_L, PIN_DIR_L);

int posR = 0;   // current position, semitones from home
int posL = 0;

uint16_t maskR = 0;   // currently latched solenoid masks
uint16_t maskL = 0;

unsigned long releaseR = 0;   // millis() timestamp for auto-release
unsigned long releaseL = 0;

String cmdBuf = "";


// ============================================================
// SHIFT REGISTER (74HC595)
// ============================================================

/*
 * Clock 16 bits into both shift register chains simultaneously.
 * SER_A feeds the right board, SER_B feeds the left board.
 * Both chains share SCK.
 * CS (latch) is pulsed once at the end to update both boards atomically.
 */
void updateBoards(uint16_t mR, uint16_t mL) {
    maskR = mR & 0x7FFFu;   // 15-bit only
    maskL = mL & 0x7FFFu;

    // Shift 16 bits, MSB first
    for (int i = 15; i >= 0; i--) {
        digitalWrite(PIN_SCK,   LOW);
        digitalWrite(PIN_SER_A, (maskR >> i) & 1u);
        digitalWrite(PIN_SER_B, (maskL >> i) & 1u);
        delayMicroseconds(1);
        digitalWrite(PIN_SCK,   HIGH);
        delayMicroseconds(1);
    }
    digitalWrite(PIN_SCK, LOW);

    // Latch both boards
    digitalWrite(PIN_CS, HIGH);
    delayMicroseconds(2);
    digitalWrite(PIN_CS, LOW);
}

inline void releaseBoard(char board) {
    if (board == 'R') updateBoards(0, maskL);
    else              updateBoards(maskR, 0);
}

inline void releaseAll() {
    updateBoards(0, 0);
}


// ============================================================
// STEPPER HELPERS
// ============================================================

void moveBoard(char board, int semitones, int rpm) {
    long target = (long)semitones * STEPS_PER_SEMITONE;
    float speed = constrain((float)rpm * STEPS_PER_SEMITONE / 60.0f,
                            200.0f, MAX_SPEED);

    if (board == 'R') {
        posR = semitones;
        stepperR.setMaxSpeed(speed);
        stepperR.moveTo(target);
    } else {
        posL = semitones;
        stepperL.setMaxSpeed(speed);
        stepperL.moveTo(target);
    }
}

void homeBoard(char board) {
    uint8_t      stopPin = (board == 'R') ? PIN_STOP_R : PIN_STOP_L;
    AccelStepper& st     = (board == 'R') ? stepperR   : stepperL;

    st.setMaxSpeed(HOME_SPEED);
    st.setAcceleration(4000.0f);
    st.move(-500000L);   // move far toward endstop

    while (digitalRead(stopPin) == HIGH) {
        st.run();
    }
    st.stop();
    st.setCurrentPosition(0);

    // Restore normal speed
    st.setMaxSpeed(MAX_SPEED);
    st.setAcceleration(ACCEL);

    if (board == 'R') posR = 0;
    else              posL = 0;

    Serial.printf("HOMED %c\n", board);
}


// ============================================================
// COMMAND PARSER
// ============================================================

void processCmd(const String& cmd) {
    if (cmd.length() == 0) return;

    // ---- MOVE R/L <offset> <rpm> ----
    if (cmd.startsWith("MOVE ") && cmd.length() > 7) {
        char  board  = cmd.charAt(5);
        int   offset = 0;
        int   rpm    = 200;
        sscanf(cmd.c_str() + 7, "%d %d", &offset, &rpm);
        moveBoard(board, offset, rpm);
        Serial.printf("OK MOVE %c %d\n", board, offset);

    // ---- FIRE R/L <0xMASK> <hold_ms> ----
    } else if (cmd.startsWith("FIRE ") && cmd.length() > 7) {
        char    board = cmd.charAt(5);
        char    maskStr[18] = {};
        int     hold  = DEFAULT_HOLD_MS;
        sscanf(cmd.c_str() + 7, "%17s %d", maskStr, &hold);
        hold = constrain(hold, 10, 2000);
        uint16_t mask = (uint16_t)strtol(maskStr, nullptr, 16);

        if (board == 'R') {
            updateBoards(mask, maskL);
            releaseR = millis() + (unsigned long)hold;
        } else {
            updateBoards(maskR, mask);
            releaseL = millis() + (unsigned long)hold;
        }
        Serial.printf("OK FIRE %c 0x%04X %d\n", board, mask, hold);

    // ---- RELEASE R/L ----
    } else if (cmd.startsWith("RELEASE ") && cmd.length() > 8) {
        char board = cmd.charAt(8);
        releaseBoard(board);
        if (board == 'R') releaseR = 0;
        else              releaseL = 0;
        Serial.printf("OK RELEASE %c\n", board);

    // ---- HOME ----
    } else if (cmd == "HOME") {
        homeBoard('R');
        homeBoard('L');
        Serial.println("OK HOME");

    // ---- STATUS ----
    } else if (cmd == "STATUS") {
        Serial.printf("STATUS R %d L %d\n", posR, posL);

    } else {
        Serial.print("ERR unknown: ");
        Serial.println(cmd);
    }
}


// ============================================================
// SETUP
// ============================================================

void setup() {
    Serial.begin(115200);

    // Shift register output pins
    pinMode(PIN_CS,    OUTPUT);  digitalWrite(PIN_CS,    LOW);
    pinMode(PIN_SCK,   OUTPUT);  digitalWrite(PIN_SCK,   LOW);
    pinMode(PIN_SER_A, OUTPUT);  digitalWrite(PIN_SER_A, LOW);
    pinMode(PIN_SER_B, OUTPUT);  digitalWrite(PIN_SER_B, LOW);

    // Clear all solenoids on startup
    releaseAll();

    // Endstop inputs
    pinMode(PIN_STOP_R, INPUT_PULLUP);
    pinMode(PIN_STOP_L, INPUT_PULLUP);

    // Stepper enable -- active LOW = steppers enabled
    pinMode(PIN_EN, OUTPUT);
    digitalWrite(PIN_EN, LOW);

    // Stepper config
    stepperR.setMaxSpeed(MAX_SPEED);
    stepperR.setAcceleration(ACCEL);
    stepperL.setMaxSpeed(MAX_SPEED);
    stepperL.setAcceleration(ACCEL);

    Serial.println("Voice2Piano Teensy ready");
}


// ============================================================
// LOOP
// ============================================================

void loop() {
    // Parse incoming serial commands
    while (Serial.available()) {
        char c = (char)Serial.read();
        if (c == '\n' || c == '\r') {
            cmdBuf.trim();
            processCmd(cmdBuf);
            cmdBuf = "";
        } else if (cmdBuf.length() < 80) {
            cmdBuf += c;
        }
    }

    // Non-blocking stepper execution
    stepperR.run();
    stepperL.run();

    // Auto-release solenoids after hold time expires
    unsigned long now = millis();
    if (releaseR && now >= releaseR) {
        releaseBoard('R');
        releaseR = 0;
    }
    if (releaseL && now >= releaseL) {
        releaseBoard('L');
        releaseL = 0;
    }
}

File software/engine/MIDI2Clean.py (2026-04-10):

"""
Voice2Piano -- MIDI2Clean.py
=============================
Layer 2a: MIDI post-processing — clean, quantise, hardware-adapt.

Takes raw MIDI from Layer 1 (pYIN / Basic Pitch) and produces a
version that is:
  1. Noise-free   (short/quiet notes removed)
  2. Quantised    (notes snapped to a rhythmic grid)
  3. Hardware-friendly (within the 15+15 solenoid range per chord)
  4. JSON-serialisable (for the Piano Roll frontend)

Endpoints (when run as server):
  POST /clean        body: {midi_b64, bpm, style, transpose}
                     returns: {melody, accomp, bpm, stats}
  POST /arrange      body: {melody, bpm, style, transpose}
                     returns: {accomp}
  POST /send_teensy  body: {accomp, bpm, transpose}
                     returns: {status}

Note format (used by PianoRoll.jsx):
  { midi: int, time: float (sec), duration: float (sec), velocity: int }
"""

import io
import base64
import json
import logging
from pathlib import Path

log = logging.getLogger("V2P-CLEAN")
logging.basicConfig(
    level=logging.INFO,
    format="%(asctime)s %(levelname)s %(message)s",
    datefmt="%H:%M:%S",
)

# ─────────────────────────────────────────────────────────────────────────────
# MIDI CLEANING
# ─────────────────────────────────────────────────────────────────────────────

# Minimum note duration to keep (seconds)
MIN_NOTE_DUR = 0.12   # raised from 0.08 — filters grace notes

# Minimum velocity to keep
MIN_VELOCITY = 30     # raised from 20 — filters ghost notes

# Quantise grid options (fraction of a beat)
GRID_OPTIONS = {
    "coarse": 1 / 2,   # half-beat
    "normal": 1 / 4,   # quarter-beat (default)
    "fine": 1 / 8,   # eighth-beat
}


def load_midi_notes(midi_bytes: bytes) -> list[dict]:
    """
    Parse a MIDI file and return a flat list of note dicts.
    Requires: pip install pretty_midi
    """
    try:
        import pretty_midi         # noqa: PLC0415
    except ImportError:
        raise RuntimeError("pip install pretty_midi")

    pm = pretty_midi.PrettyMIDI(io.BytesIO(midi_bytes))
    notes = []
    for inst in pm.instruments:
        if inst.is_drum:
            continue
        for n in inst.notes:
            notes.append({
                "midi": n.pitch,
                "time": round(n.start, 4),
                "duration": round(n.end - n.start, 4),
                "velocity": n.velocity,
            })
    notes.sort(key=lambda n: n["time"])
    return notes


def remove_noise(notes: list[dict]) -> list[dict]:
    """
    Drop notes that are too short or too quiet to be intentional.
    """
    return [
        n for n in notes
        if n["duration"] >= MIN_NOTE_DUR and n["velocity"] >= MIN_VELOCITY
    ]


def quantise(
    notes: list[dict],
    bpm: float,
    grid: str = "normal",
) -> list[dict]:
    """
    Snap note start times and durations to the nearest rhythmic grid point.
    Grid is expressed as a fraction of a beat (e.g. 1/4 = sixteenth note).
    """
    beat_sec = 60.0 / max(bpm, 1)
    step = beat_sec * GRID_OPTIONS.get(grid, GRID_OPTIONS["normal"])

    result = []
    for n in notes:
        snapped_start = round(n["time"] / step) * step
        snapped_dur = max(step, round(n["duration"] / step) * step)
        result.append({
            **n,
            "time": round(snapped_start, 4),
            "duration": round(snapped_dur, 4),
        })
    return result


def clamp_to_hardware(notes: list[dict]) -> list[dict]:
    """
    Clamp MIDI pitches to A0-C8 (21-108), the full piano range.
    Notes outside this range are octave-shifted into range.
    """
    out = []
    for n in notes:
        midi = n["midi"]
        while midi < 21:
            midi += 12
        while midi > 108:
            midi -= 12
        out.append({**n, "midi": midi})
    return out


def apply_transpose(notes: list[dict], semitones: int) -> list[dict]:
    """Shift all notes by semitones, then clamp to range."""
    shifted = [{**n, "midi": n["midi"] + semitones} for n in notes]
    return clamp_to_hardware(shifted)


def assess_playability(notes: list[dict]) -> dict:
    """
    Check how hardware-friendly a set of notes is.
    Each 'chord' (notes within 50ms of each other) should span ≤15 semitones
    so one board can cover it, or ≤30 semitones across both boards.
    Returns a dict with stats and a playability score 0-1.
    """
    if not notes:
        return {"score": 1.0, "chords": 0, "problem_chords": 0}

    # Group simultaneous notes (within 50ms)
    groups = []
    buf = [notes[0]]
    for n in notes[1:]:
        if n["time"] - buf[0]["time"] < 0.05:
            buf.append(n)
        else:
            groups.append(buf)
            buf = [n]
    if buf:
        groups.append(buf)

    problem = 0
    for g in groups:
        midis = [n["midi"] for n in g]
        span = max(midis) - min(midis)
        if span > 30:   # can't cover with both boards
            problem += 1

    score = 1.0 - (problem / max(len(groups), 1))
    return {
        "score": round(score, 3),
        "chords": len(groups),
        "problem_chords": problem,
    }
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

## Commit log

2026-03-03 Hardware/PCB: Completed and finalized the PCB layout for fabrication.
    [BOM.csv, Driver_Board_Left.kicad_sch, Driver_Board_Right.kicad_sch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]
2026-03-03 Updated .gitignore for KiCad 9.0 and macOS development to ensure only core design files and libraries are tracked, while keeping the repository free of temporary backups, logs, and system junk.
2026-03-23 Completed Layer 2 pipeline, firmware, and project documentation
    Layer 2 (Python, host):
    - add MIDI2Chords.py: Krumhansl key detection, Markov chord sequencer,
    melody-affinity voicing, corpus training via --train flag
    - add MIDI2Piano.py: rail planner, Teensy serial driver, sim fallback
    Firmware (Teensy 4.1, PlatformIO):
    - add firmware/src/main.cpp: solenoid control via 74HC595 shift registers,
    dual stepper (AccelStepper), MOVE/FIRE/RELEASE/HOME/STATUS protocol
    - add firmware/platformio.ini: teensy41 board, AccelStepper dependency
    Software fixes:
    - fix FileMode.jsx: stale closure white screen crash on mixed source upload
    - fix Vocal2MIDI_file.py: FileNotFoundError from premature tmp_dir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
    [MIDI2Chords.py, MIDI2Piano.py, Vocal2MIDI_file.py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]
2026-04-06 Fix: Strip heavy deps for Railway 4GB limit, voice-only server.
    [Vocal2MIDI_file.py]
2026-04-06 Railway deployment, capability detection, and Flake8 cleanup
    Backend:
    - add Railway deployment config (Procfile, requirements.txt, nixpacks.toml)
    - update health endpoint to return capabilities/server_mode/limits
    auto-detects full vs lite mode based on installed dependencies
    Frontend:
    - FileMode v8: fetch /health on mount, grey out unavailable source
    options with tooltip, show lite-mode banner when on Railway server
    - remove duplicate LiveMode version files
    Engine:
    - fix Vocal2MIDI_file.py: asyncio.get_event_loop() → get_running_loop(),
    lambda closure in run_in_executor replaced with named function
    - fix MIDI2Chords.py: all Flake8 errors (E221 E231 E501 E741 E702)
    - fix Vocal2MIDI_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
    [Vocal2MIDI_file.py]
2026-04-06 Deployed to Vercel + Railway; added capability detection and lite-mode UI.
2026-04-10 Updated website to visualize solenoids' movements.
